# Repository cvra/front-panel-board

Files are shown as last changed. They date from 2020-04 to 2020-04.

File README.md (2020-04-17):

# Front Panel PCB

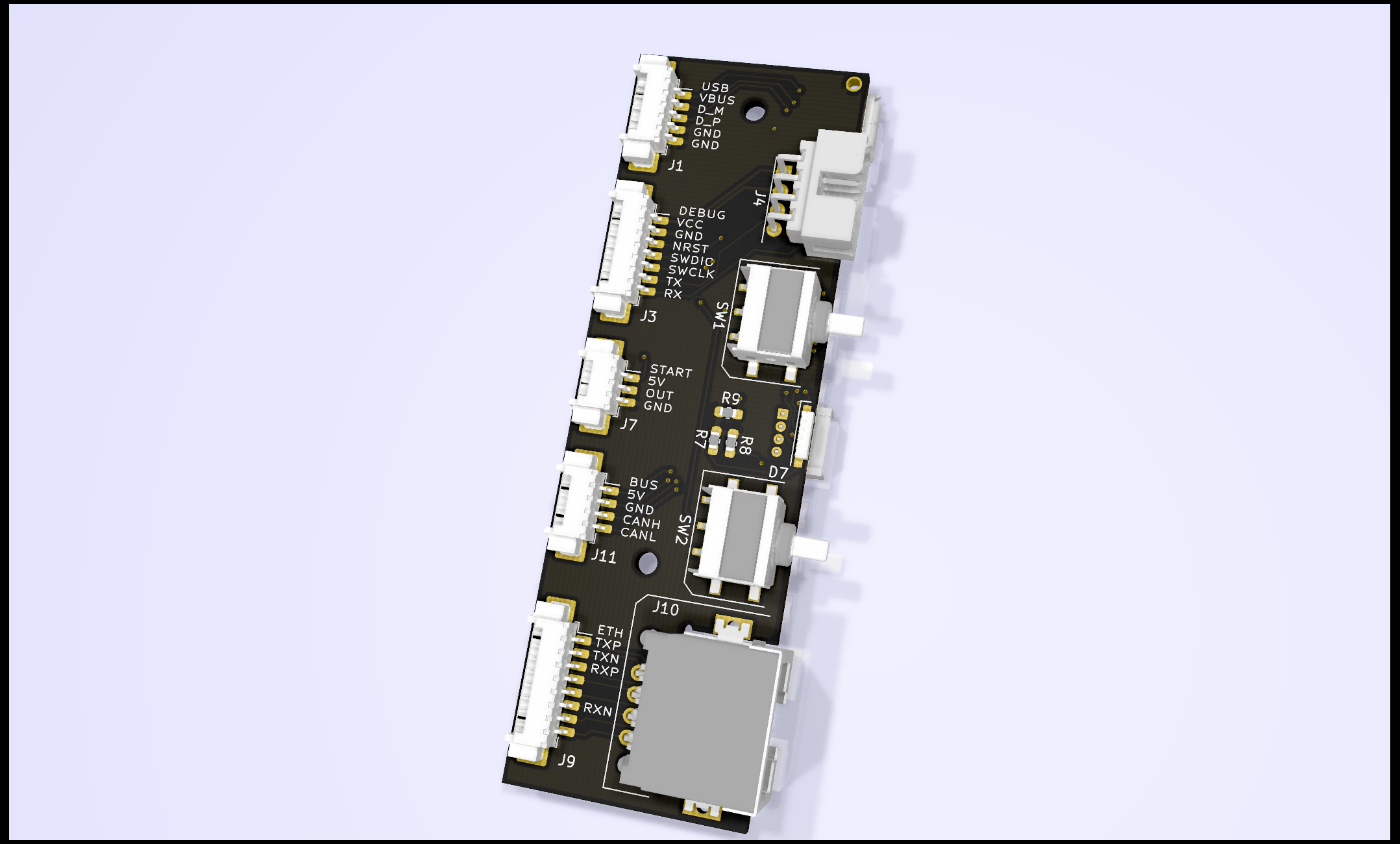
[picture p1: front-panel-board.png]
CAD view of the board

Board dimensions

This small PCB is used to expose debug and HMI signals from inside the robot to
the external world through a front panel. The main goal is to simplify the
wiring and have a sturdy mount.

## Requirements

* USB Forwarding: Picoblade -> USB
* Ethernet forwarding: Picoblade -> RJ45
* CVRA debug forwarding
* CAN forwardig
* 6 LEDS + Team selection indication (RGB)
* 2 buttons for team selection
* Connector for the hall sensor starter: 5V, Signal, GND
* One connector to the nucleo shield for all GPIOs
* Max width: 80 mm, but lower is better
* Max length: 30mm
* Connectors must be at least 1.5mm off the board to go through the panel
* The board height should be as symmetrical as possible
* 2xM2 mounting holes.
* SWDIO exposed through something sturdier than Picoblade used in the past
* The silkscreen should document pinout to simplify troubleshooting

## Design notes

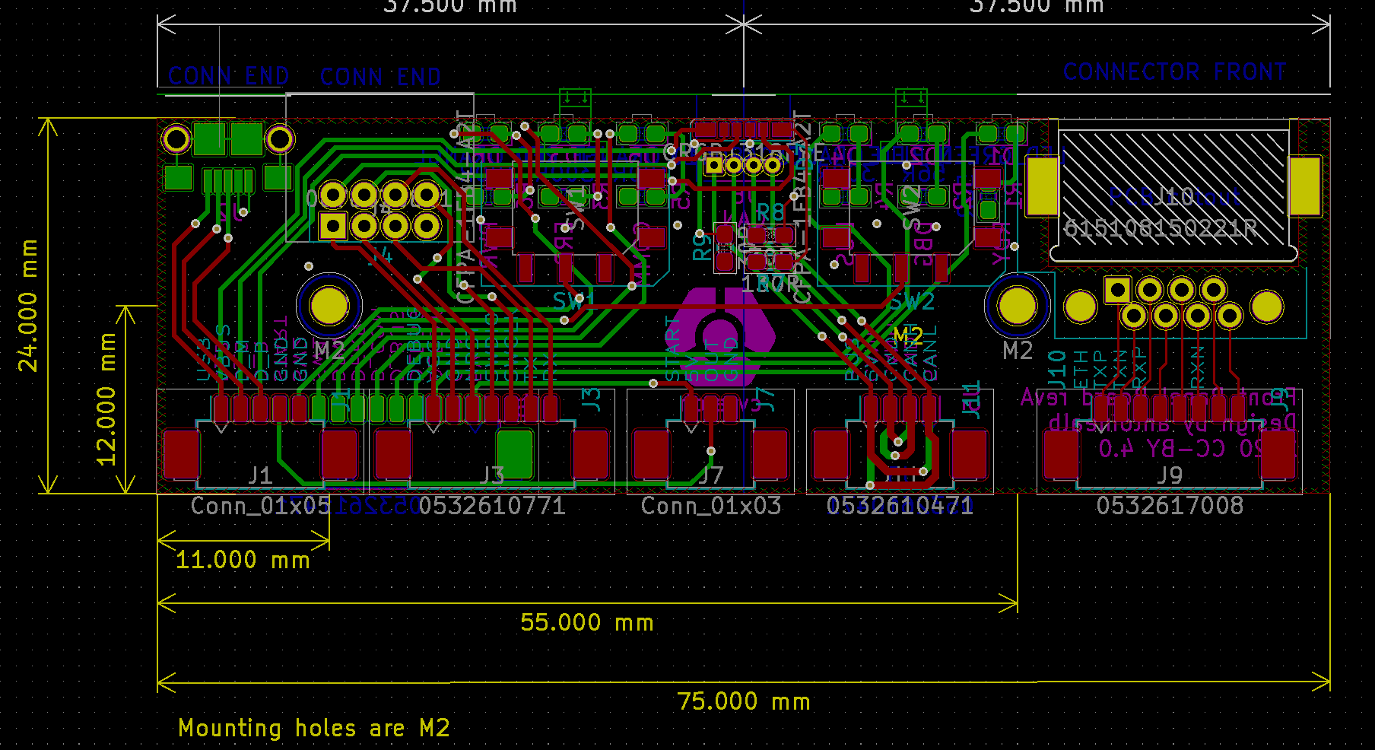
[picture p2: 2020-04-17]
board_dimensions.png

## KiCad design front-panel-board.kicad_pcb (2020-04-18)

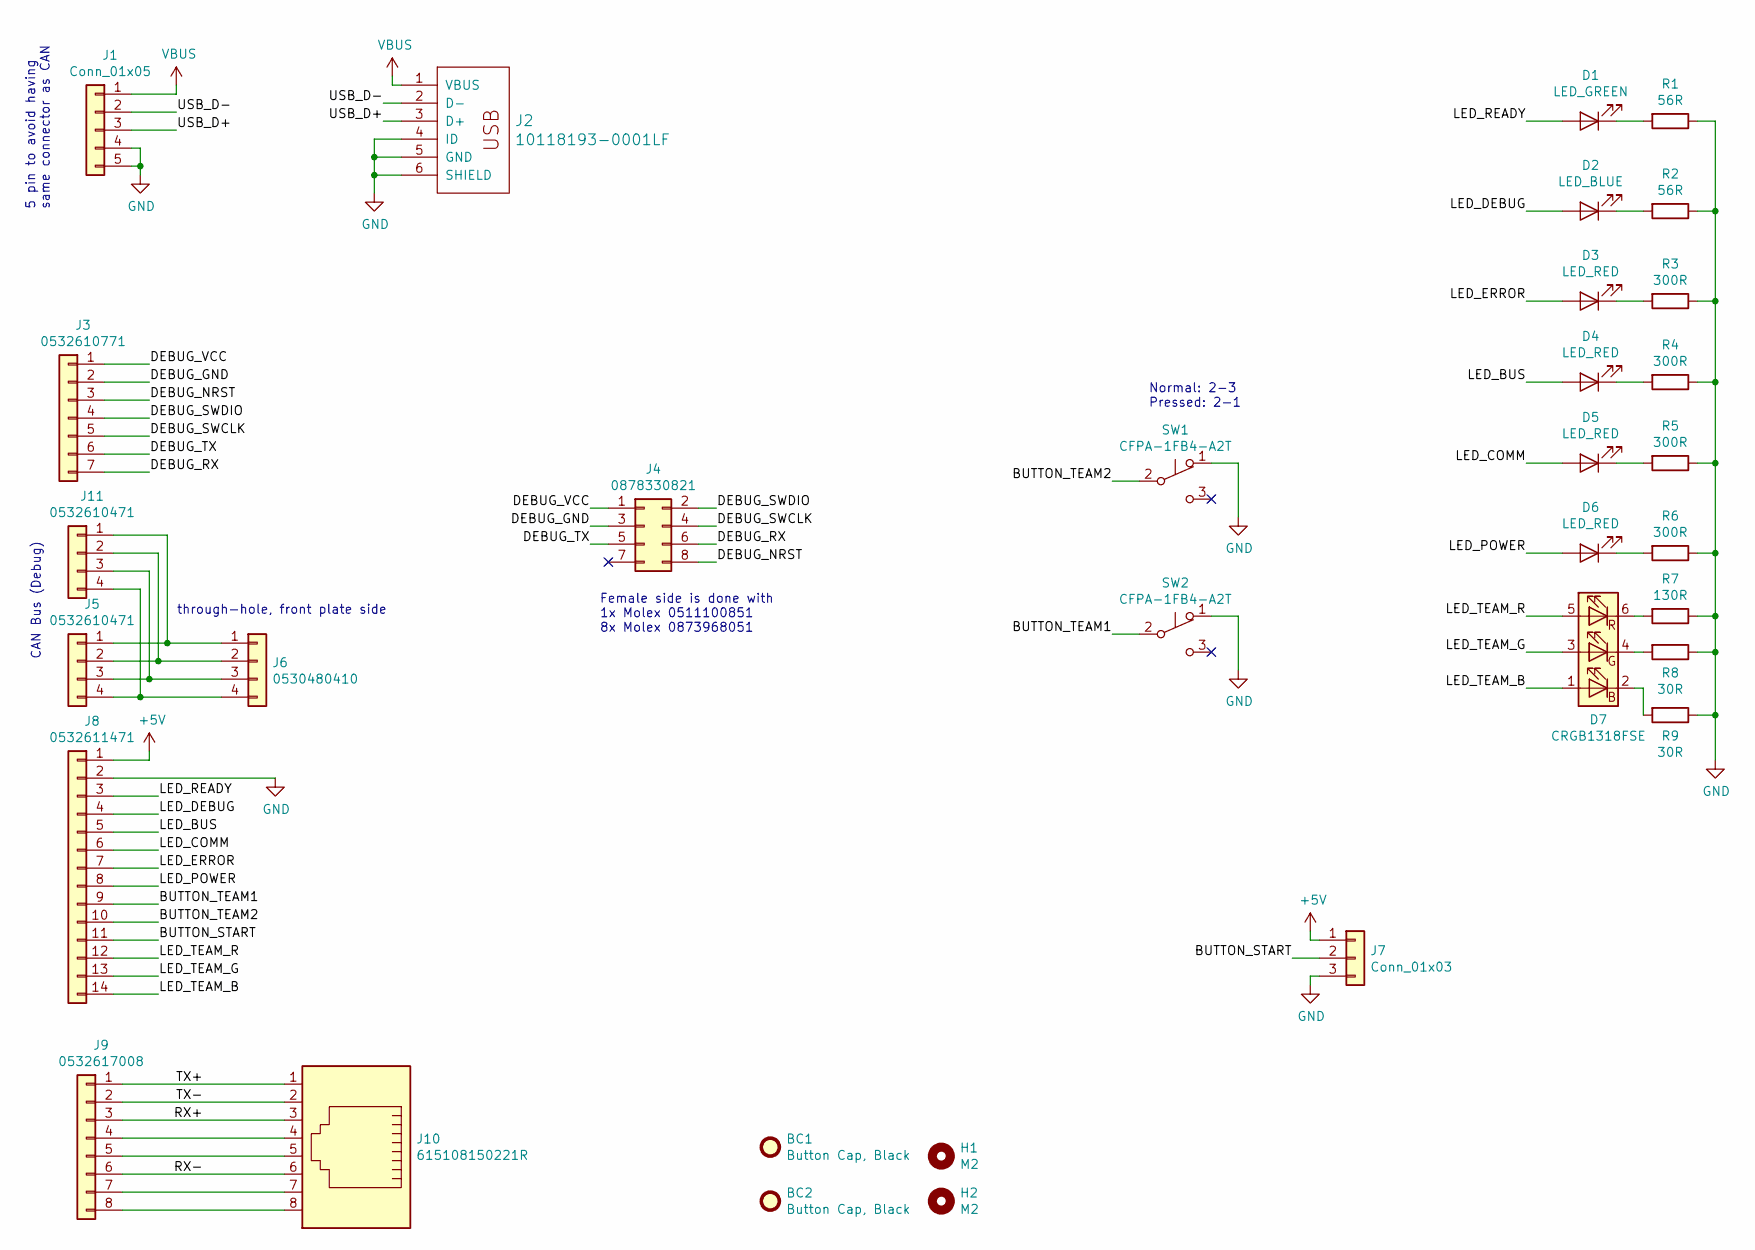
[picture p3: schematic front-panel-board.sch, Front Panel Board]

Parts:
BC1, BC2: Button Cap, Black; digikey# 563-1179-ND
D1: LED_GREEN; LED_0603_RightAngle; digikey# 160-1475-1-ND
D2: LED_BLUE; LED_0603_RightAngle; digikey# 1830-1029-1-ND
D3: LED_RED; LED_0603_RightAngle; digikey# 160-1479-1-ND
D4, D5, D6: LED_RED; LED_0603_RightAngle
D7: CRGB1318FSE; CRGB1318FSE-TM; digikey# 404-1264-1-ND
H1, H2: M2; MountingHole_2.2mm_M2_ISO14580
J1: Conn_01x05; Molex_PicoBlade_53261-0571_1x05-1MP_P1.25mm_Horizontal; digikey# WM7623CT-ND
J2: 10118193-0001LF; _Micro-USB-AB-receptacle-SMT-th-no-slot; digikey# 609-4616-1-ND
J3: 0532610771; Molex_PicoBlade_53261-0771_1x07-1MP_P1.25mm_Horizontal; digikey# WM7625CT-ND
J4: 0878330821; 0878330821_02x03_pin_header; digikey# WM23634-ND
J5, J11: 0532610471; Molex_PicoBlade_53261-0471_1x04-1MP_P1.25mm_Horizontal; digikey# WM7622TR-ND
J6: 0530480410; Molex-PicoBlade-4-Edge; digikey# WM1744-ND
J7: Conn_01x03; Molex_PicoBlade_53261-0371_1x03-1MP_P1.25mm_Horizontal; digikey# WM7621CT-ND
J8: 0532611471; Molex_PicoBlade_53261-1471_1x14-1MP_P1.25mm_Horizontal; digikey# WM7631CT-ND
J9: 0532617008; Molex_PicoBlade_53261-0871_1x08-1MP_P1.25mm_Horizontal; digikey# WM26501CT-ND
J10: 615108150221R; 615108150221R_Ethernet_MiddleMount; digikey# 732-13727-1-ND
R1: 56R; R_0603_1608Metric_Pad1.05x0.95mm_HandSolder; digikey# 311-56.0HRCT-ND
R2: 56R; R_0603_1608Metric_Pad1.05x0.95mm_HandSolder
R3: 300R; R_0603_1608Metric_Pad1.05x0.95mm_HandSolder; digikey# 311-300HRCT-ND
R4, R5, R6: 300R; R_0603_1608Metric_Pad1.05x0.95mm_HandSolder
R7: 130R; R_0603_1608Metric_Pad1.05x0.95mm_HandSolder; digikey# 311-130HRCT-ND
R8: 30R; R_0603_1608Metric_Pad1.05x0.95mm_HandSolder; digikey# 311-30.0HRCT-ND
R9: 30R; R_0603_1608Metric_Pad1.05x0.95mm_HandSolder
SW1, SW2: CFPA-1FB4-A2T; digikey# 563-1246-1-ND

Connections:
+5V: J7.1, J8.1
/BUTTON_START: J7.2, J8.11
/BUTTON_TEAM1: J8.9, SW2.2 (B)
/BUTTON_TEAM2: J8.10, SW1.2 (B)
/DEBUG_GND: J3.2, J4.3
/DEBUG_NRST: J3.3, J4.8
/DEBUG_RX: J3.7, J4.6
/DEBUG_SWCLK: J3.5, J4.4
/DEBUG_SWDIO: J3.4, J4.2
/DEBUG_TX: J3.6, J4.5
/DEBUG_VCC: J3.1, J4.1
/LED_BUS: D4.2 (A), J8.5
/LED_COMM: D5.2 (A), J8.6
/LED_DEBUG: D2.2 (A), J8.4
/LED_ERROR: D3.2 (A), J8.7
/LED_POWER: D6.2 (A), J8.8
/LED_READY: D1.2 (A), J8.3
/LED_TEAM_B: D7.1 (BA), J8.14
/LED_TEAM_G: D7.3 (GA), J8.13
/LED_TEAM_R: D7.5 (RA), J8.12
/RX+: J9.3, J10.3
/RX-: J9.6, J10.6
/TX+: J9.1, J10.1
/TX-: J9.2, J10.2
/USB_D+: J1.3, J2.3 (D+)
/USB_D-: J1.2, J2.2 (D-)
GND: J1.4, J1.5, J2.4 (ID), J2.5 (GND), J2.6 (SHIELD), J7.3, J8.2, R1.1, R2.1, R3.1, R4.1, R5.1, R6.1, R7.1, R8.1, R9.1, SW1.1 (A), SW2.1 (A)
unnamed: D1.1 (K), R1.2
unnamed: D2.1 (K), R2.2
unnamed: D3.1 (K), R3.2
unnamed: D4.1 (K), R4.2
unnamed: D5.1 (K), R5.2
unnamed: D6.1 (K), R6.2
unnamed: D7.2 (BK), R9.2
unnamed: D7.4 (GK), R8.2
unnamed: D7.6 (RK), R7.2
unnamed: J9.4, J10.4
unnamed: J9.5, J10.5
unnamed: J9.7, J10.7
unnamed: J9.8, J10.8
unnamed: J5.1, J6.1, J11.1
unnamed: J5.2, J6.2, J11.2
unnamed: J5.3, J6.3, J11.3
unnamed: J5.4, J6.4, J11.4
VBUS: J1.1, J2.1 (VBUS)

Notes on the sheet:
Normal: 2-3 Pressed: 2-1
through-hole, front plate side
CAN Bus (Debug)
5 pin to avoid having same connector as CAN
Female side is done with 1x Molex 0511100851 8x Molex 0873968051

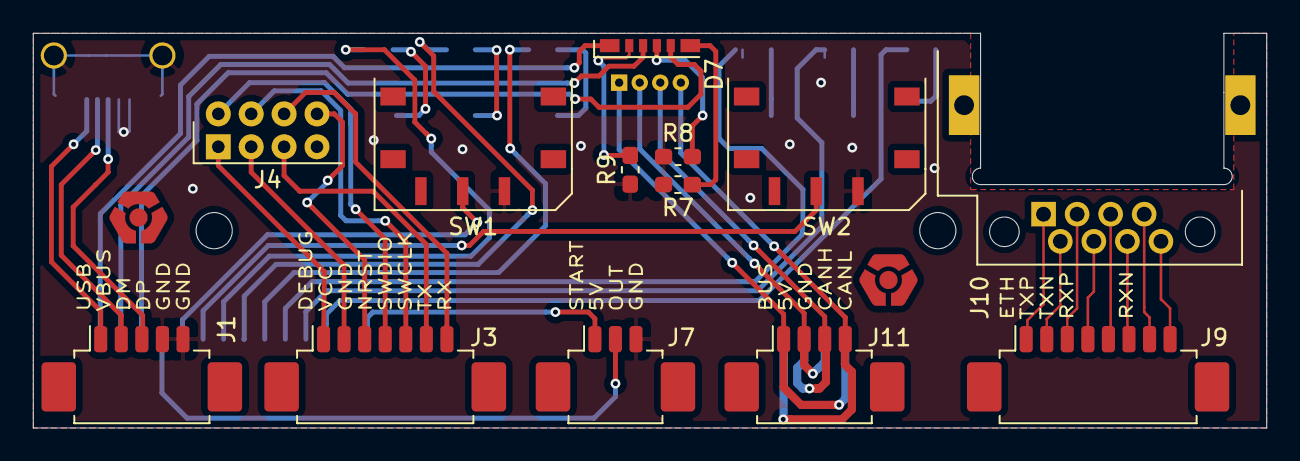
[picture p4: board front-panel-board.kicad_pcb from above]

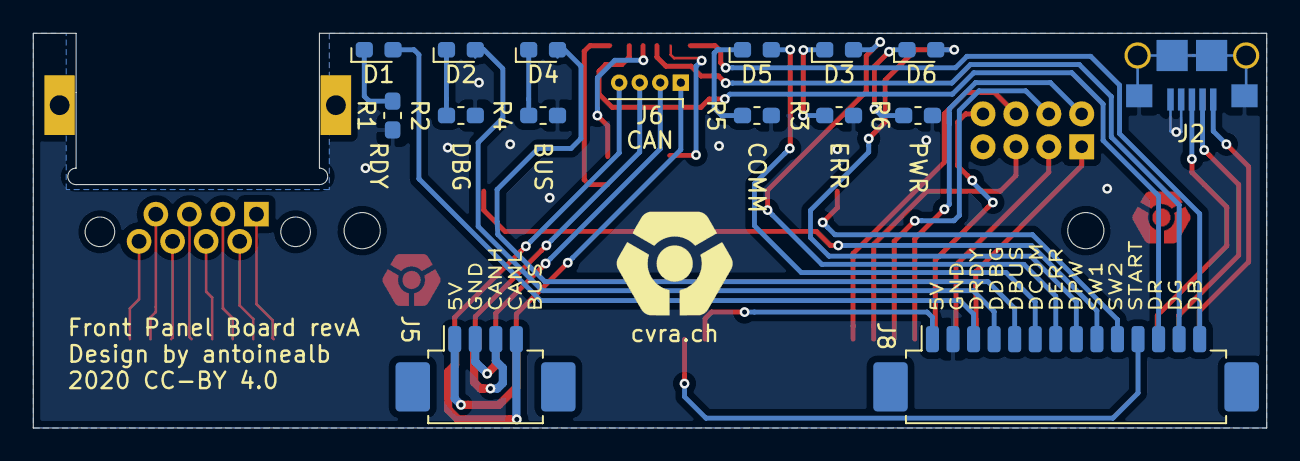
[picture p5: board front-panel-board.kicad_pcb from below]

Board: 2 copper layers, 75.0 x 24.0 mm, 31 parts (16 on the bottom side), 45 nets.

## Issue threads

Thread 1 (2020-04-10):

Initial review of the PCB

antoinealb, 2020-04-10:
Creating an issue for the review of the finished work. If you guys have time, would be great.

nuft, 2020-04-11:
Quelques remarques:
* Si possible ajoute les 3dshapes dans le projet (pas forcément dans kicad-lib)
* Vu que les connecteurs CAN sont prévus d'être daisychained je mettrais une trace plus grande (~0.5mm)
* le placement des mounting holes a l'air un peu aléatoire. c'est bien pour l'intégration mécanique? Tu peux aussi documenter les côtes sur (Dwgs.User ou Cmts.User) et un screenshot dans le readme.

antoinealb, 2020-04-11:
> Si possible ajoute les 3dshapes dans le projet (pas forcément dans kicad-lib)

Out of curiosity, c'est quoi l'idée derrière? Parce que dans le style guide ils mettent le footprint et la 3dshape ensemble.

> Vu que les connecteurs CAN sont prévus d'être daisychained je mettrais une trace plus grande (~0.5mm)

Ok, j'ai bump les traces de power

> le placement des mounting holes a l'air un peu aléatoire. c'est bien pour l'intégration mécanique?

Romain a dit que je pouvais le mettre ou je voulais, donc j'ai mis là ou ca ne gêne pas le layout.

nuft, 2020-04-11:
> Ok, j'ai bump les traces de power

Je mettrai aussi plus sur les lignes de CAN.

> c'est quoi l'idée derrière?

Pour que ça soit complet. Comme ça il faut pas les chercher sur internet pour une v2 ou un autre projet.

> Parce que dans le style guide ils mettent le footprint et la 3dshape ensemble.

Peu importe ou tu places les 3dshapes. J'aimerais que c'est packaged avec le projet.

Closed 2020-04-17.

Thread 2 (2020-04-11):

Board review with my remarks

vieillemaison, 2020-04-11:
Schematics:
There is still the remark TODO for the RGB led?

PCB:
General:
- Try in general to no go to the smallest track width and isolation distance if it's not clearly needed (it could increase PCB costs and the tracks are more fragile.
- Avoid big openings in the ground plane and never in the same area (potential EMC problems) you can solve the issue by rerouting a little bit some tracks and by adding some vias
- Change ground plane roules to reduce the track width (to much heat lost and potential problem with hand welding)

USB connector:
- Routing of tracks need to be done from bottom.
- Avoid the connection between pins but do it outside even if it's GND
- Silkscreen is smaller than the others and there is also the component value that is normally disabled

D5:
- one pad track entry could be rerouted (not so clean ;-))

J8:
- Text of debug LED signals are not on the right pins

Closed 2020-04-17.

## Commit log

2020-03-15 Empty project
    [front-panel-board.kicad_pcb, front-panel-board.sch]
2020-03-15 Add cvra kicad lib
2020-03-19 Basic schematic
    [front-panel-board.sch]
2020-03-19 Update kicad-lib
2020-04-10 First revision of the front panel board
    [front-panel-board.kicad_pcb, front-panel-board.sch]
2020-04-17 Fixes after PCB review
    * Bump trace width to 0.3 mm everywhere (except RJ45 conn)
    * Bump clearance to 0.2 mm everywhere (except RJ45 conn)
    * Reduced thermal relief width
    * Improved ground plane
    * Cleaned up USB connector routing / silkscreen
    * Moved mechanical elements after review by mechanical engineering.
    * Fixed connector labeling
    * Bigger traces on CAN connectors for daisy chain
    Fixes #1
    Fixes #2
    [front-panel-board.kicad_pcb, front-panel-board.sch]
2020-04-17 Add board dimensions to README
2020-04-17 Use red LEDs instead of orange ones, as they are OoS
    [front-panel-board.sch]
2020-04-17 Add notes on female programming cable manufacturing
    [front-panel-board.sch]
2020-04-18 Minor fixes
    * Add a CVRA logo in copper
    * Move around some tracks
    * Make more tracks 0.3mm
    [front-panel-board.kicad_pcb]

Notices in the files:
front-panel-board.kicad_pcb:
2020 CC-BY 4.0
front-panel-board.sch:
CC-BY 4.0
